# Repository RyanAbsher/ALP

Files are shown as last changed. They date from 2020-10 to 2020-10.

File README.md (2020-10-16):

# ALP

A wireless control system for a balloon-based aerial cave photography lighting platform.

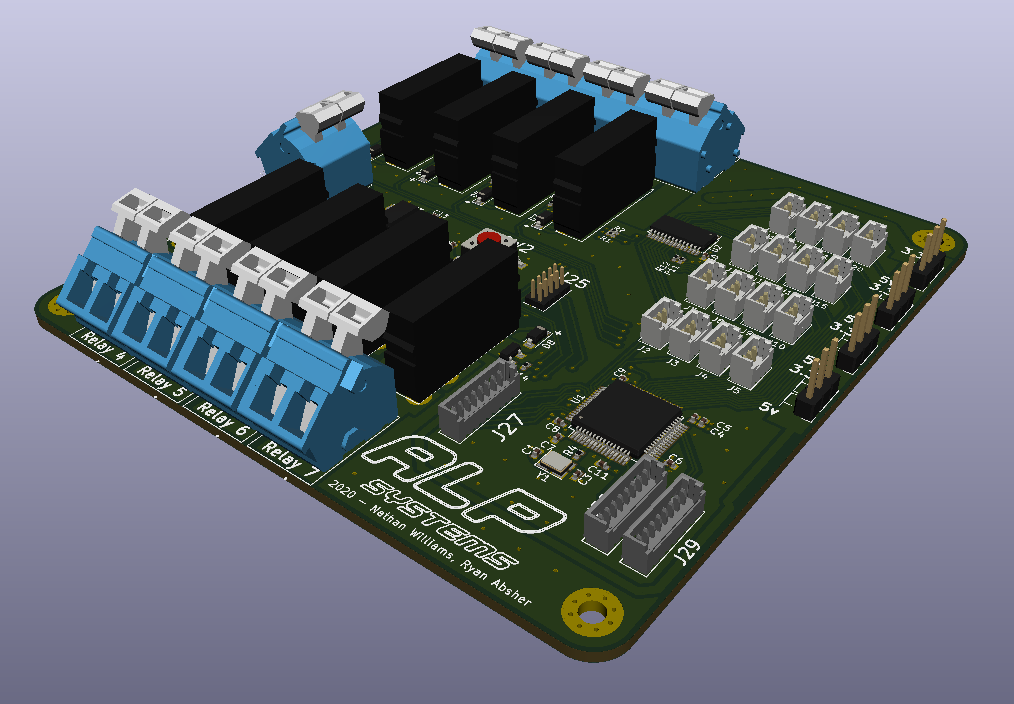
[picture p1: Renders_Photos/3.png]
PCB Render


## Introduction
A friend of mine has for a long time wanted to photograph the top of a particular cave chamber that has never been photographed before. The chamber is 396 feet tall, so access to the top is obviously somewhat limited. In the past they have used a 6' diameter weather balloon to lift lighting to the top, then used telephoto lenses to photograph it from the ground. This time they are putting the cameras on the balloon, but they didn't have a good way to control the equipment from the ground. This project is the solution to that problem.

## Hardware
The board is based on an STM32 microcontroller. There are three different boards needed for this project: 1 on the ballon, and 2 in control boxes on the ground. I have designed this PCB so that the same design can be used for all of the locations. It is also generic enough that it can be adapted if this particular project changes, or if we want to use it for other projects in the future. There are 8 dedicated relay outputs (5A DC Max) and 16 general IO connectors. These can be used as inputs or outputs, and each bank of 4 connectors has a jumper that can be used to select either 5v or 3.3v outputs. Each of these 16 outputs can also optionally be used as a servo output, with a dedicated servo driver IC on-board.

Communication between boards is accomplished using USART. The two control boxes are connected with a cable. The balloon-mounted board uses HC-12 serial radio modules to communicate with the primary control box on the ground. In ground-based tests of these radios we have achieved effective communication over distances greater than 1400 meters. I do not anticipate any problem using them to communicated over ~120 meters.

Users on the ground can use the two control boxes to control various equipment on the balloon. There is a DSLR camera mounted on the balloon, and the ISO, Aperture, and Shutter speed can be set from the ground. The shutter can of course also be triggered from the ground. The DSLR is mounted on a custom pan/tilt servo gimbal, and this is fully controllable from the ground.

There are 3 powerful LED lights mounted on the balloon, these are controlled through some of the relay outputs, and their direction can be controlled with a servo attached to each.

There are various other pieces of hardware that are controllable from the ground, although the configuration and type of such is likely to change as the project continues.

## Prototype
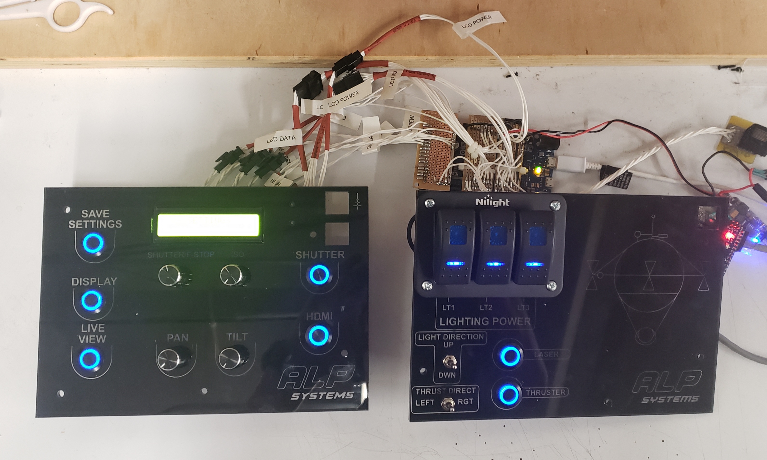
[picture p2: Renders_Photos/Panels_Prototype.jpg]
PCB Render

The photo above contains the laser-etched acrylic control panels, and the stripboard working prototype that I built. While it admittedly doesn't look that great, it did serve it's purpose in that it showed all of the pieces of the system could communicate and function as expected.

## To Do
I have an STM32 dev board on the way that has the same chip that I will be using on this board (STM32F103RBT6). I will use it to confirm that it can do everything I expect of it, then I will be ordering the PCBs. I will likely be ordering them from JLCPCB, and will have them assemble the SMT components on at least a few of the boards. The boards will be populated differently depending on which location they are currently in. For example, the control boxes will not need the relays populated. I will hand-solder the relays and connectors as needed.

Once I have the boards in hand, then I can write the necessary software. I programmed the protoype using the Arduino environment, and I was happy with the way the software worked. Since I have the software mostly completed, it should be fairly simple to port it over to the STM32, likely using STs STM32CubeIDE software. When the software is complete, I will add it to this repository.

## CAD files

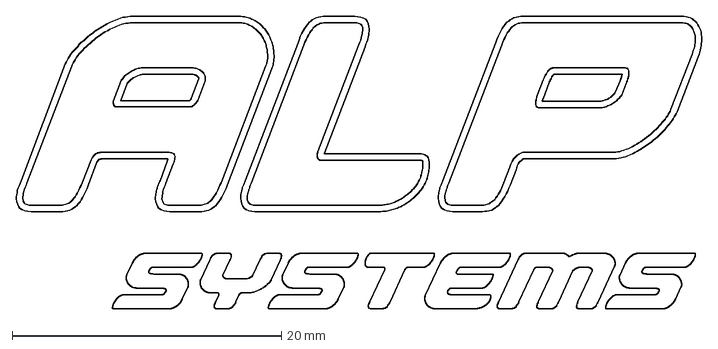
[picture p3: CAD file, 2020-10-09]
logo.dxf
50.9 x 21.7 mm

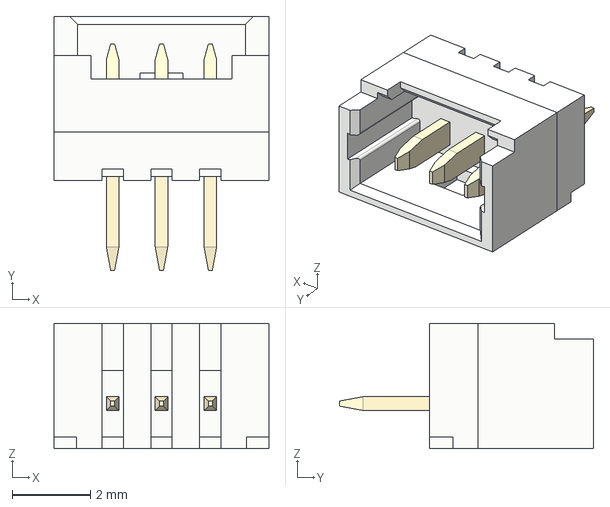
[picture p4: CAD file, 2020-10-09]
Models/Molex_Picoblade_530470310.stp
5.50 x 6.50 x 3.20 mm

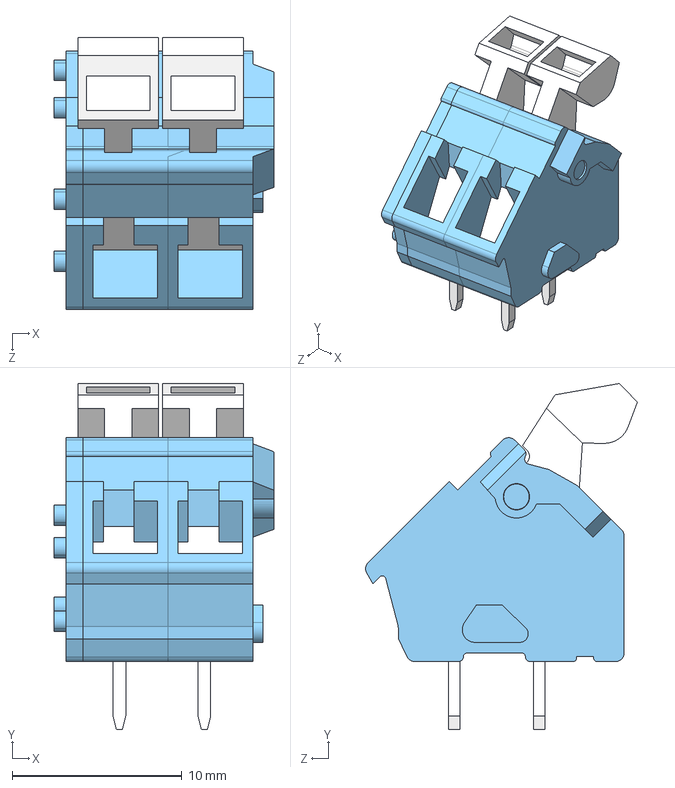
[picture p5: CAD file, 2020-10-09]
Models/CUI_DEVICES_TBL005A-500-02BE-2WT.step
12.9 x 20.4 x 16.0 mm
TBL005A-500 - END CAP_Blue
TBL005A-500 - BODY_Blue x 2
TBL005A-500 - PUSH BUTTON_White x 2

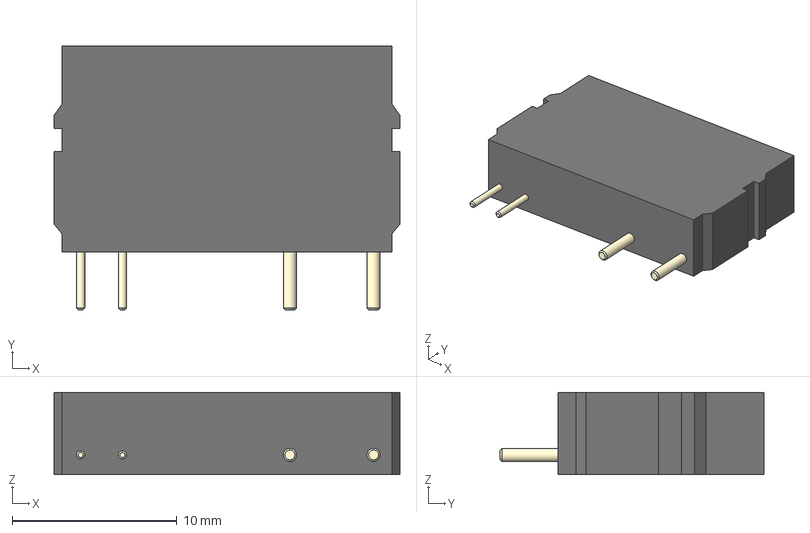
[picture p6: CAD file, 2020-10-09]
Models/APAN3103.step
21.0 x 16.0 x 5.00 mm

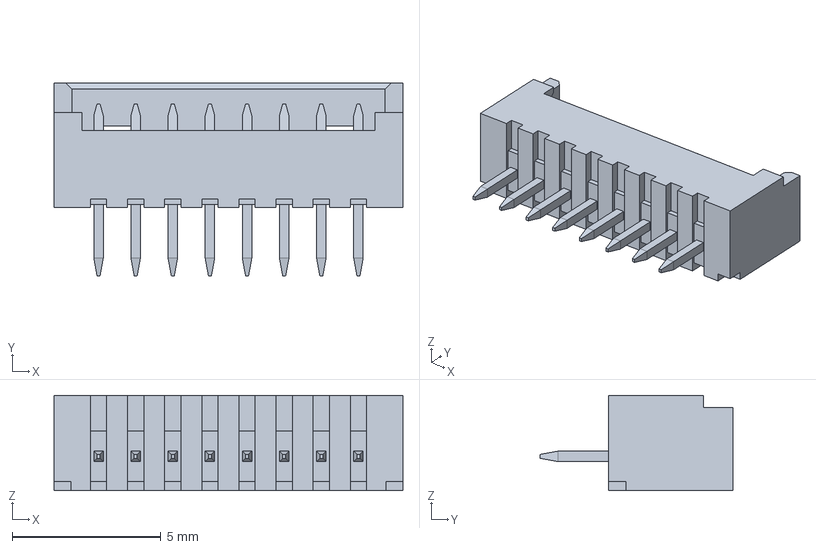
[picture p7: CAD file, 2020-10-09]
Models/Molex_Picoblade_530470810.stp
11.8 x 6.50 x 3.20 mm

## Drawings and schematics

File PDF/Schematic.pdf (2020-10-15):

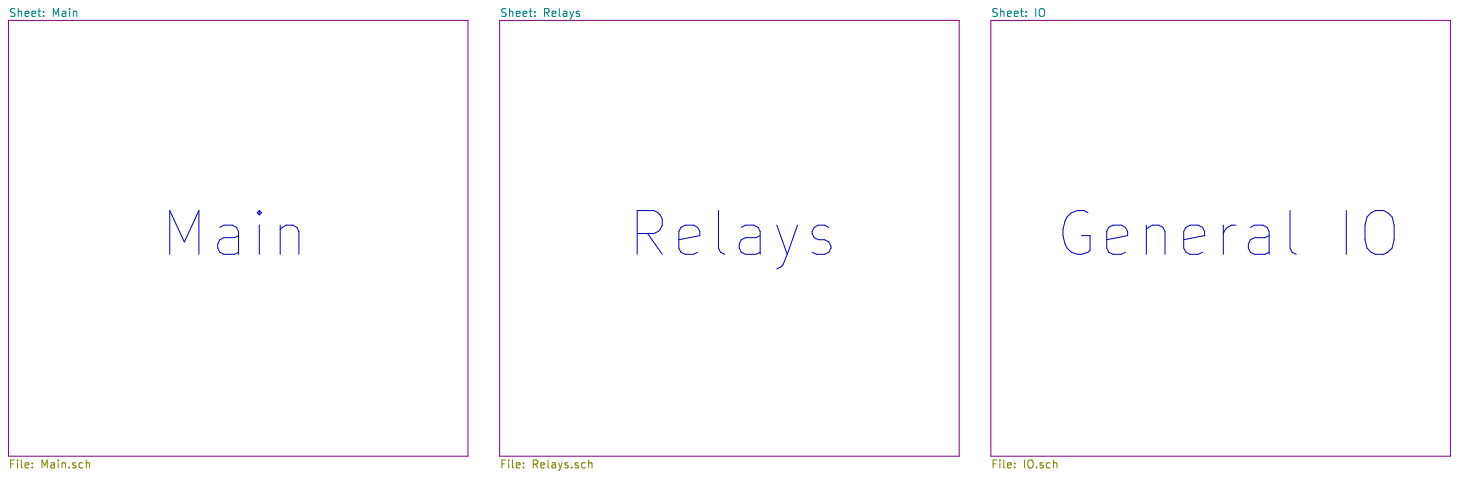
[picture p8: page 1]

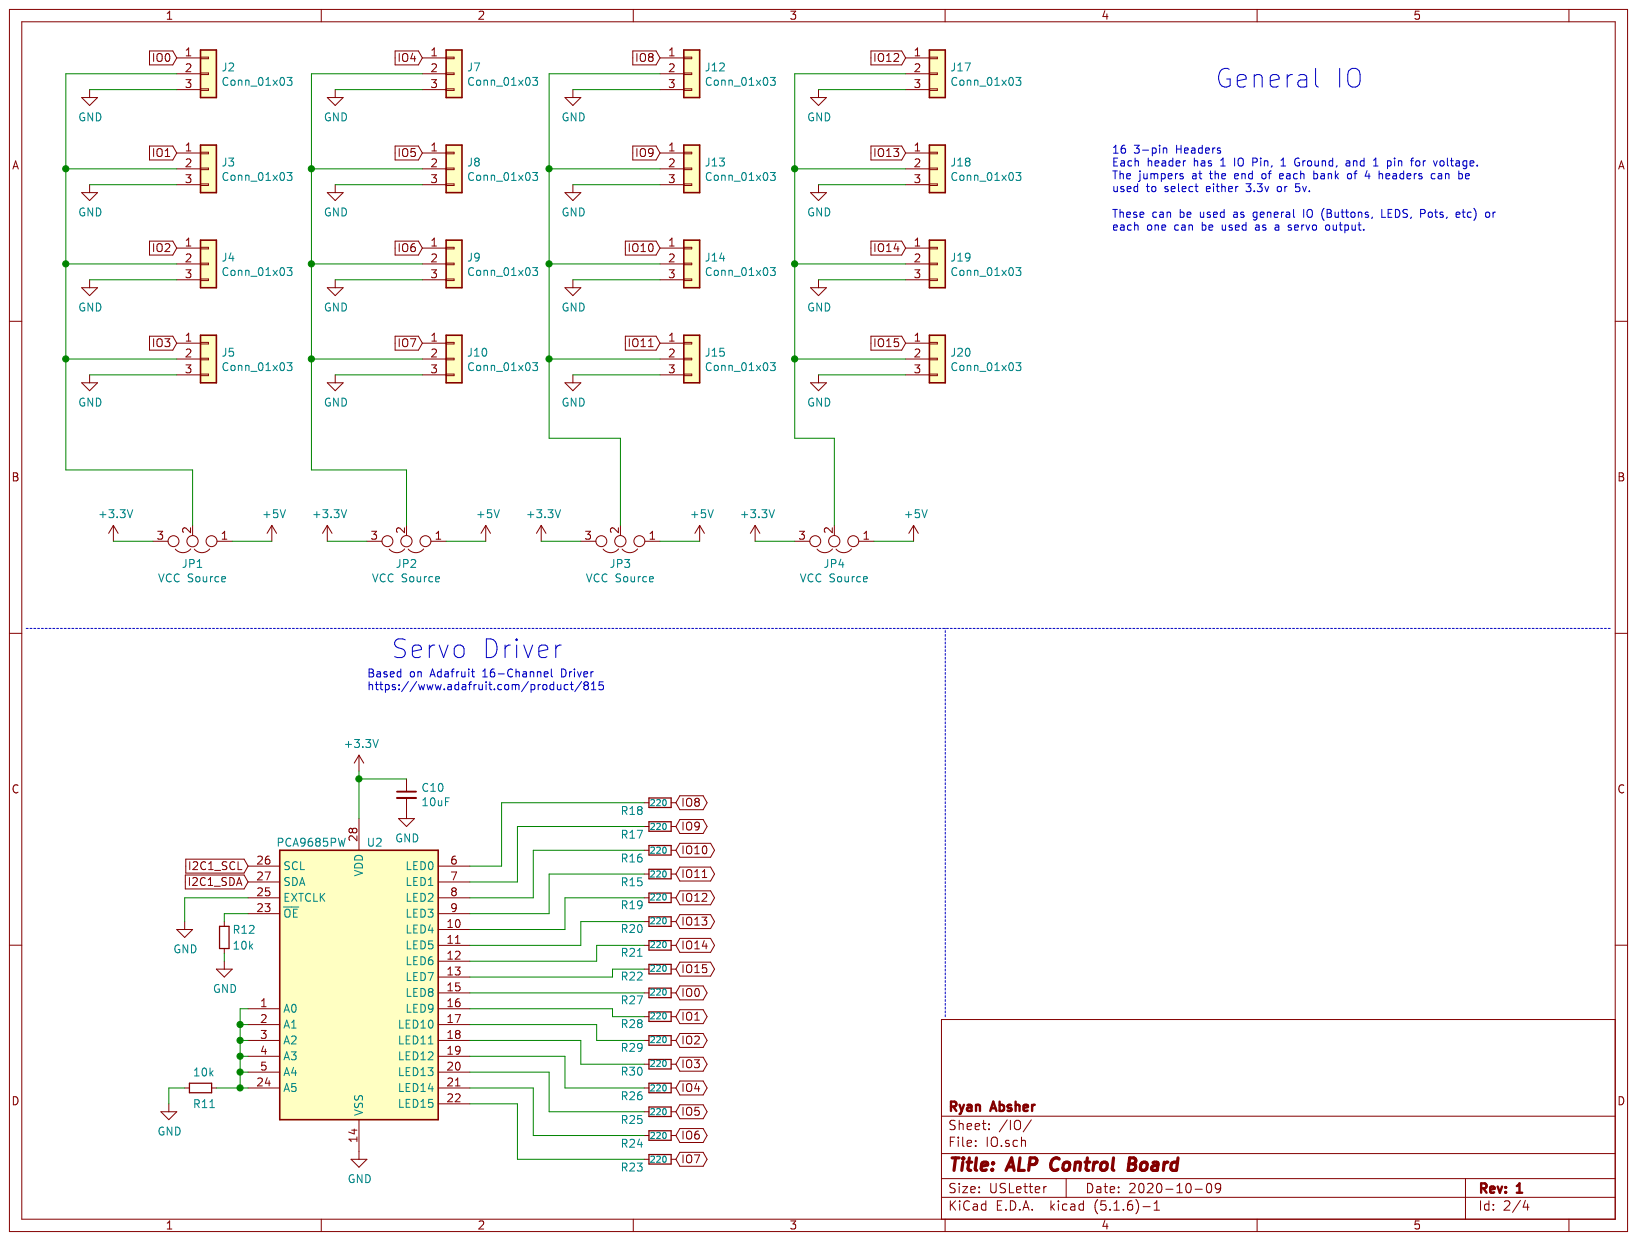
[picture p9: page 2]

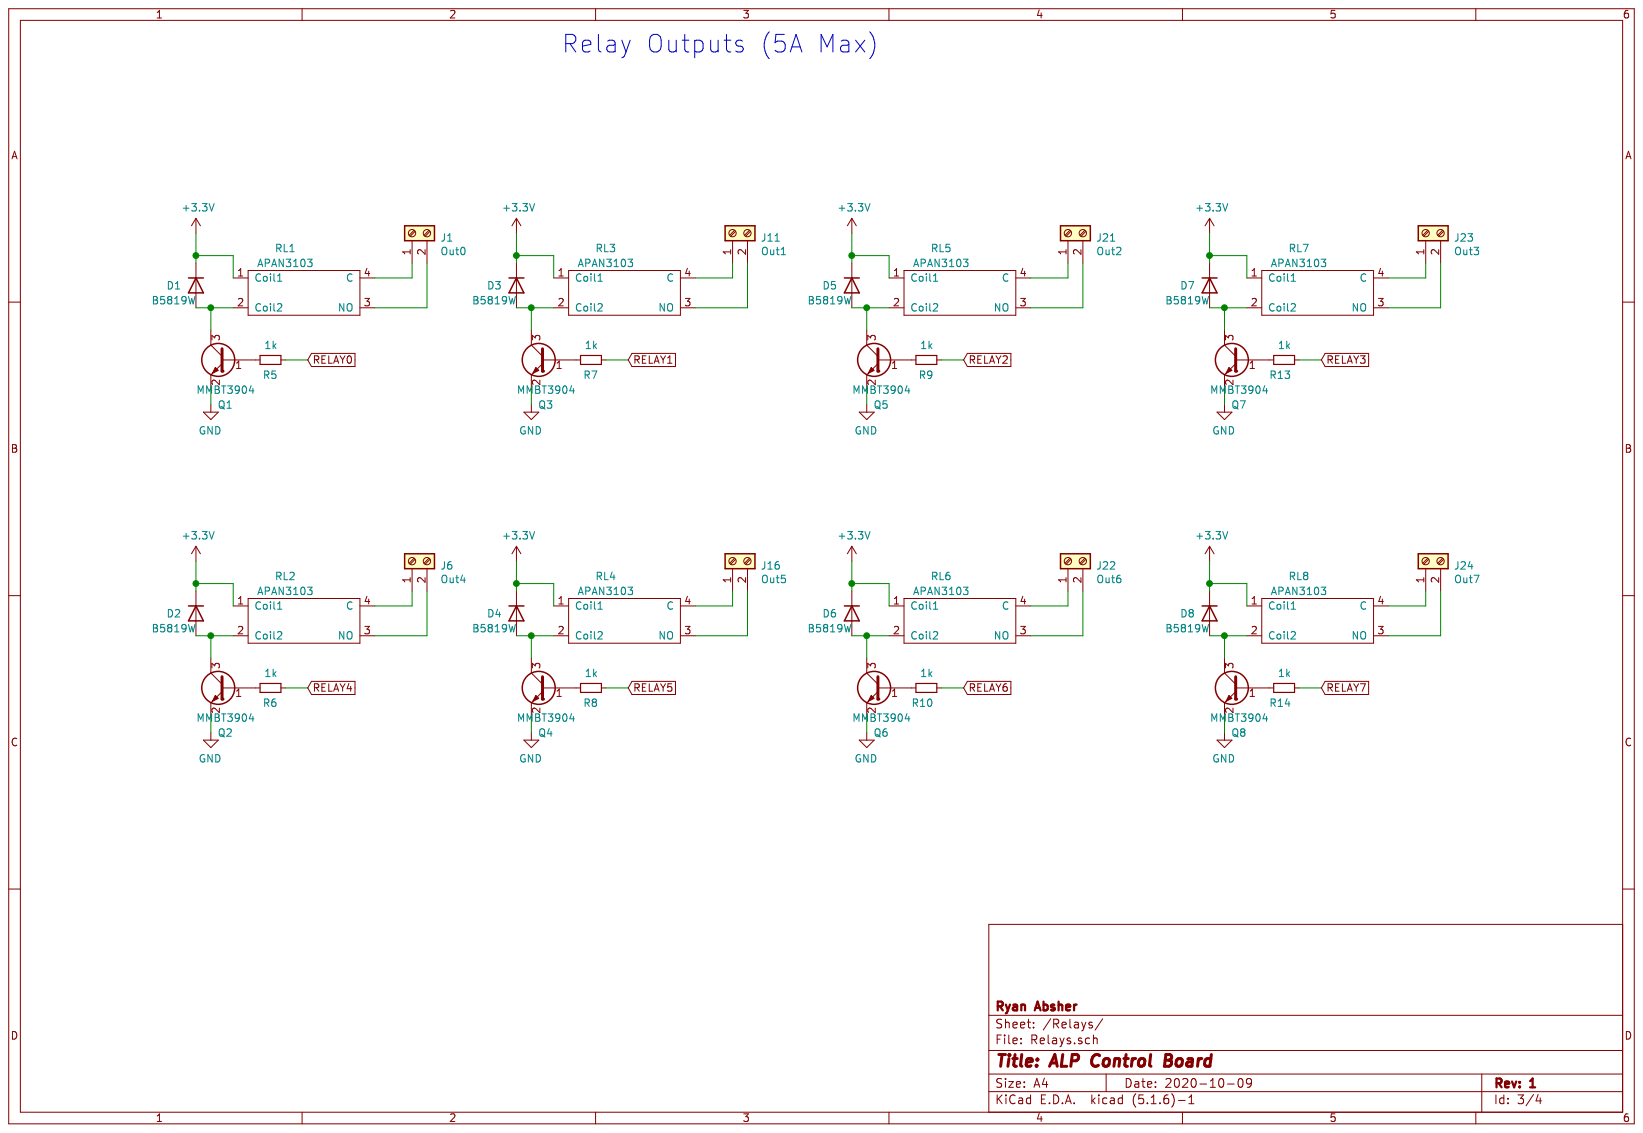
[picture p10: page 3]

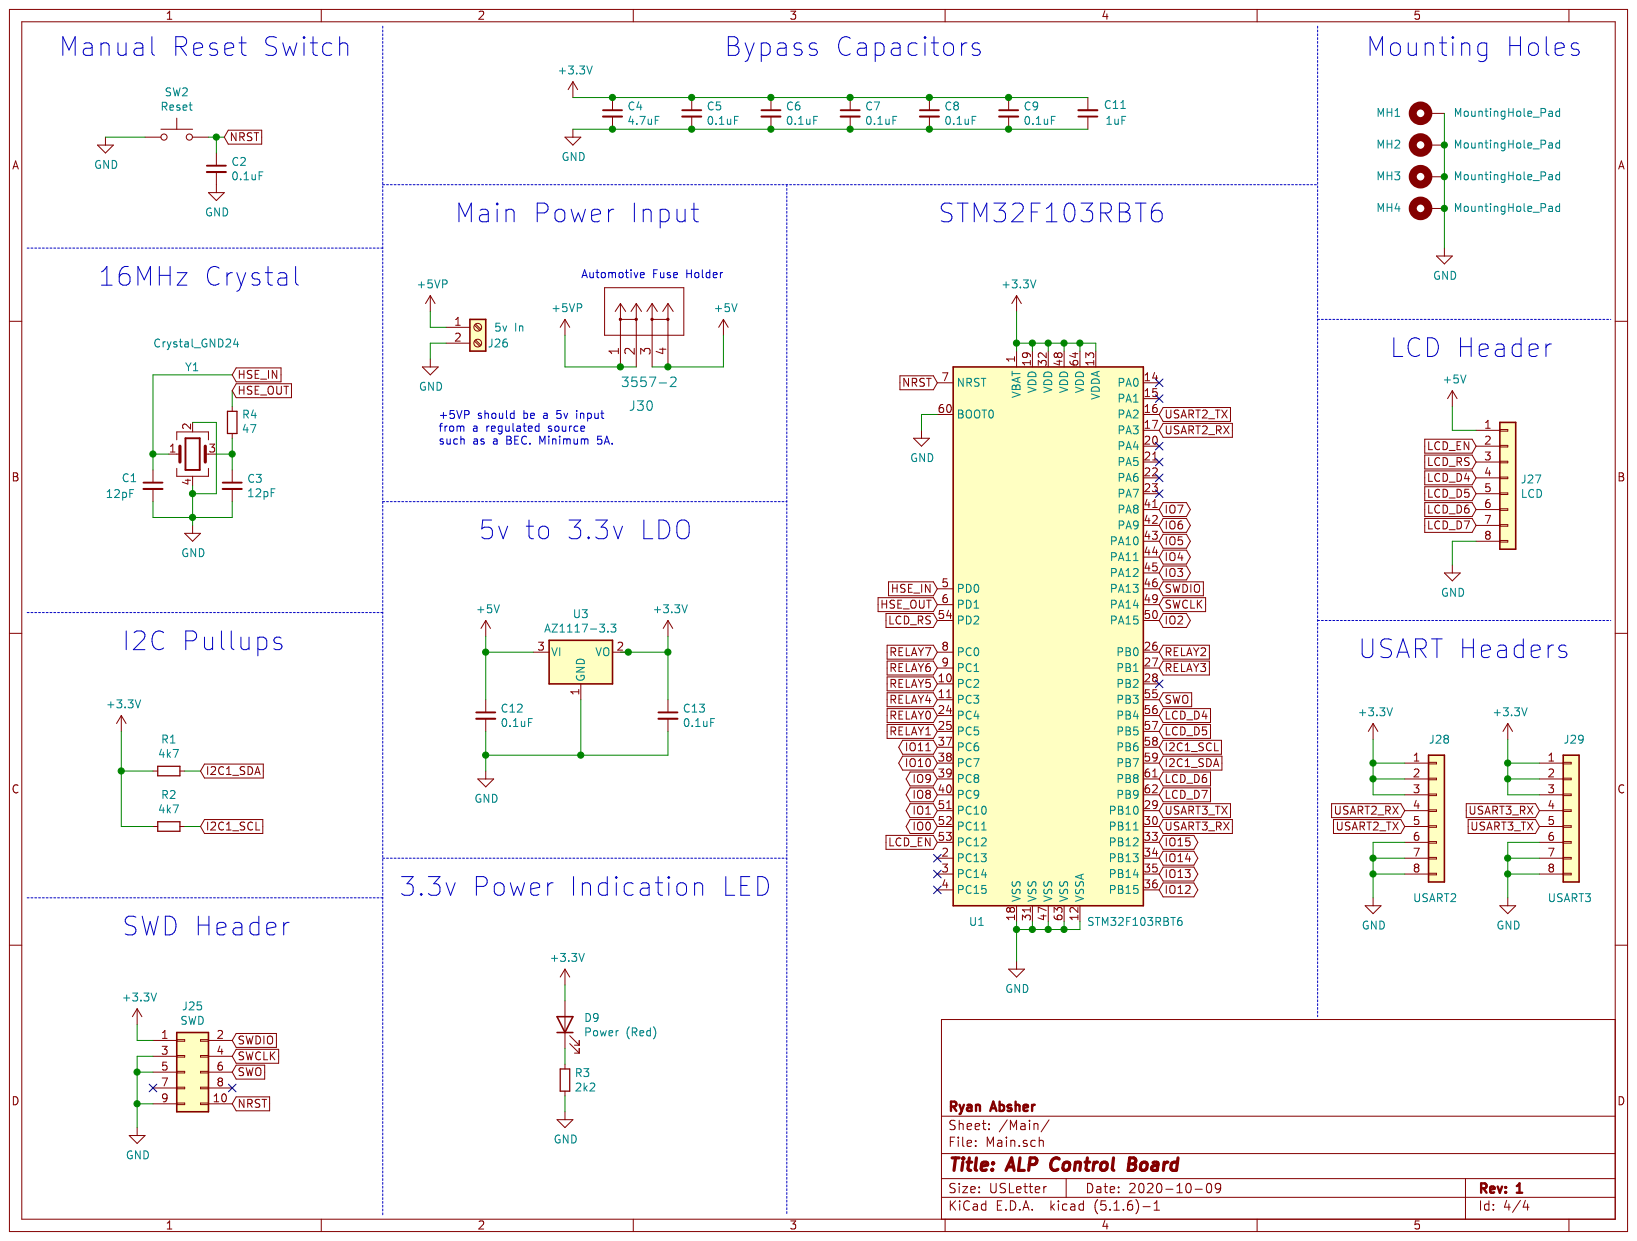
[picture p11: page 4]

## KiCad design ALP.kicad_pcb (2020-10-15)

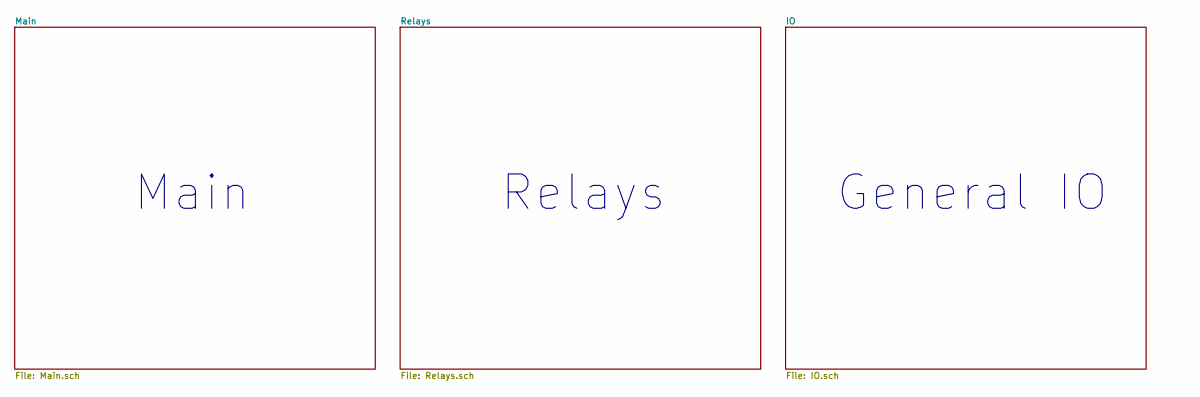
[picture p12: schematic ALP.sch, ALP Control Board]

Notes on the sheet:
General IO
Main
Relays

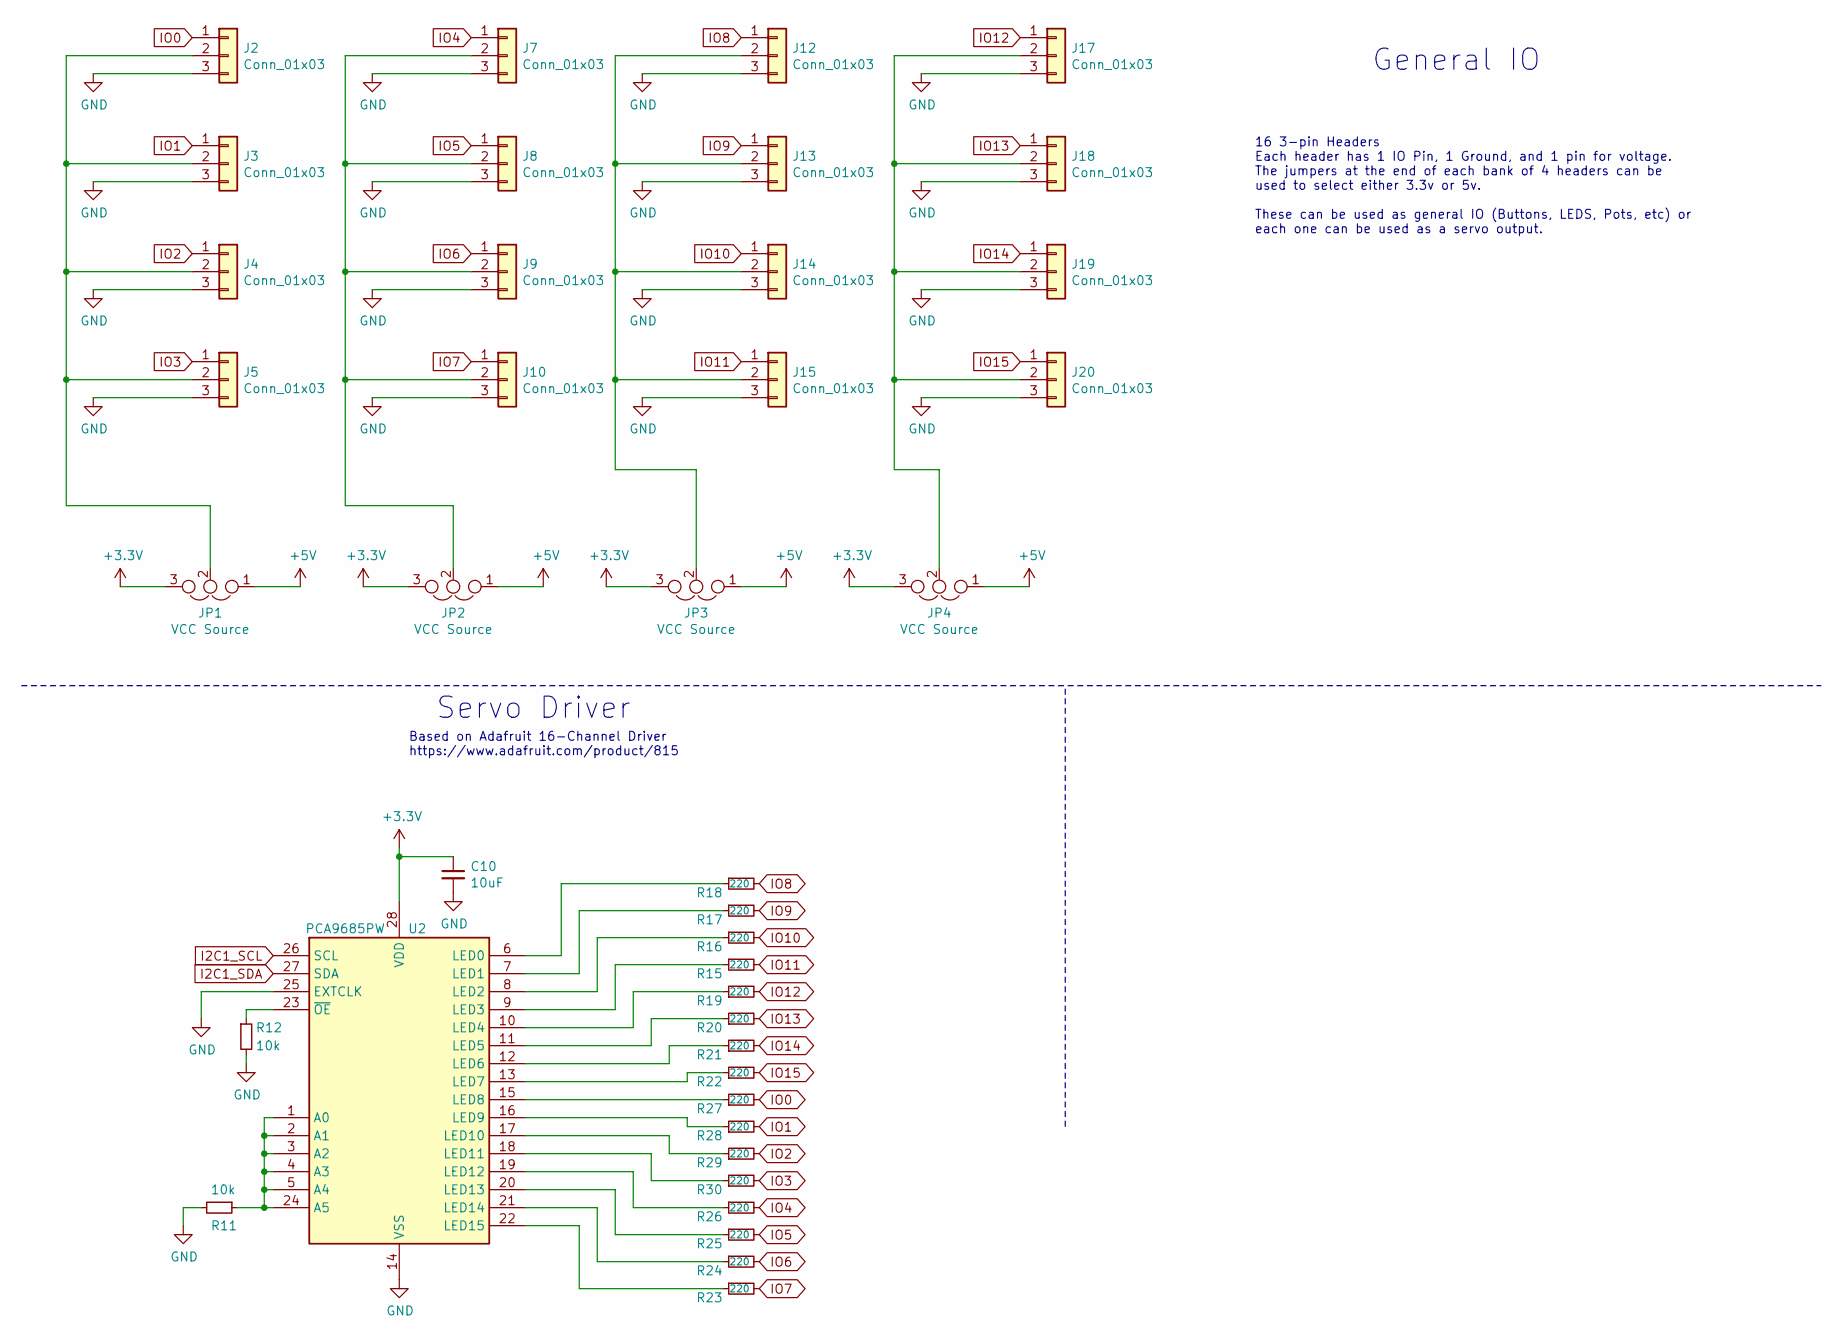
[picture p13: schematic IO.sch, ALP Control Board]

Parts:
C10: 10uF; C_0402_1005Metric; LCSC Part # C15525
J2, J3, J4, J5, J7, J8, J9, J10, J12, J13, J14, J15, J17, J18, J19, J20: Conn_01x03; Molex_PicoBlade_53047-0610_1x03_P1.25mm_Vertical
JP1, JP2, JP3, JP4: VCC Source; PinHeader_1x03_P2.54mm_Vertical
R11, R12: 10k; R_0402_1005Metric; LCSC Part # C25744
R15, R16, R17, R18, R19, R20, R21, R22, R23, R24, R25, R26, R27, R28, R29, R30: 220; R_0402_1005Metric; LCSC Part # C1555
U2: PCA9685PW; TSSOP-28_4.4x9.7mm_P0.65mm; LCSC Part # C92206

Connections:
+3V3: C10.1, JP1.3, JP2.3, JP3.3, JP4.3, U2.28 (VDD); also elsewhere on the board
+5V: JP1.1, JP2.1, JP3.1, JP4.1; also elsewhere on the board
GND: C10.2, J2.3, J3.3, J4.3, J5.3, J7.3, J8.3, J9.3, J10.3, J12.3, J13.3, J14.3, J15.3, J17.3, J18.3, J19.3, J20.3, R11.2, R12.2, U2.14 (VSS), U2.25 (EXTCLK); also elsewhere on the board
I2C1_SCL: U2.26 (SCL); also elsewhere on the board
I2C1_SDA: U2.27 (SDA); also elsewhere on the board
IO0: J2.1, R27.2; also elsewhere on the board
IO1: J3.1, R28.2; also elsewhere on the board
IO2: J4.1, R29.2; also elsewhere on the board
IO3: J5.1, R30.2; also elsewhere on the board
IO4: J7.1, R26.2; also elsewhere on the board
IO5: J8.1, R25.2; also elsewhere on the board
IO6: J9.1, R24.2; also elsewhere on the board
IO7: J10.1, R23.2; also elsewhere on the board
IO8: J12.1, R18.2; also elsewhere on the board
IO9: J13.1, R17.2; also elsewhere on the board
IO10: J14.1, R16.2; also elsewhere on the board
IO11: J15.1, R15.2; also elsewhere on the board
IO12: J17.1, R19.2; also elsewhere on the board
IO13: J18.1, R20.2; also elsewhere on the board
IO14: J19.1, R21.2; also elsewhere on the board
IO15: J20.1, R22.2; also elsewhere on the board
unnamed: J2.2, J3.2, J4.2, J5.2, JP1.2
unnamed: J7.2, J8.2, J9.2, J10.2, JP2.2
unnamed: J12.2, J13.2, J14.2, J15.2, JP3.2
unnamed: J17.2, J18.2, J19.2, J20.2, JP4.2
unnamed: R11.1, U2.1 (A0), U2.2 (A1), U2.3 (A2), U2.4 (A3), U2.5 (A4), U2.24 (A5)
unnamed: R12.1, U2.23 (~OE)
unnamed: R15.1, U2.9 (LED3)
unnamed: R16.1, U2.8 (LED2)
unnamed: R17.1, U2.7 (LED1)
unnamed: R18.1, U2.6 (LED0)
unnamed: R19.1, U2.10 (LED4)
unnamed: R20.1, U2.11 (LED5)
unnamed: R21.1, U2.12 (LED6)
unnamed: R22.1, U2.13 (LED7)
unnamed: R23.1, U2.22 (LED15)
unnamed: R24.1, U2.21 (LED14)
unnamed: R25.1, U2.20 (LED13)
unnamed: R26.1, U2.19 (LED12)
unnamed: R27.1, U2.15 (LED8)
unnamed: R28.1, U2.16 (LED9)
unnamed: R29.1, U2.17 (LED10)
unnamed: R30.1, U2.18 (LED11)

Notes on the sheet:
Servo Driver
Based on Adafruit 16-Channel Driver https://www.adafruit.com/product/815
16 3-pin Headers Each header has 1 IO Pin, 1 Ground, and 1 pin for voltage. The jumpers at the end of each bank of 4 headers can be used to select either 3.3v or 5v. These can be used as general IO (Buttons, LEDS, Pots, etc) or each one can be used as a servo output.
General IO

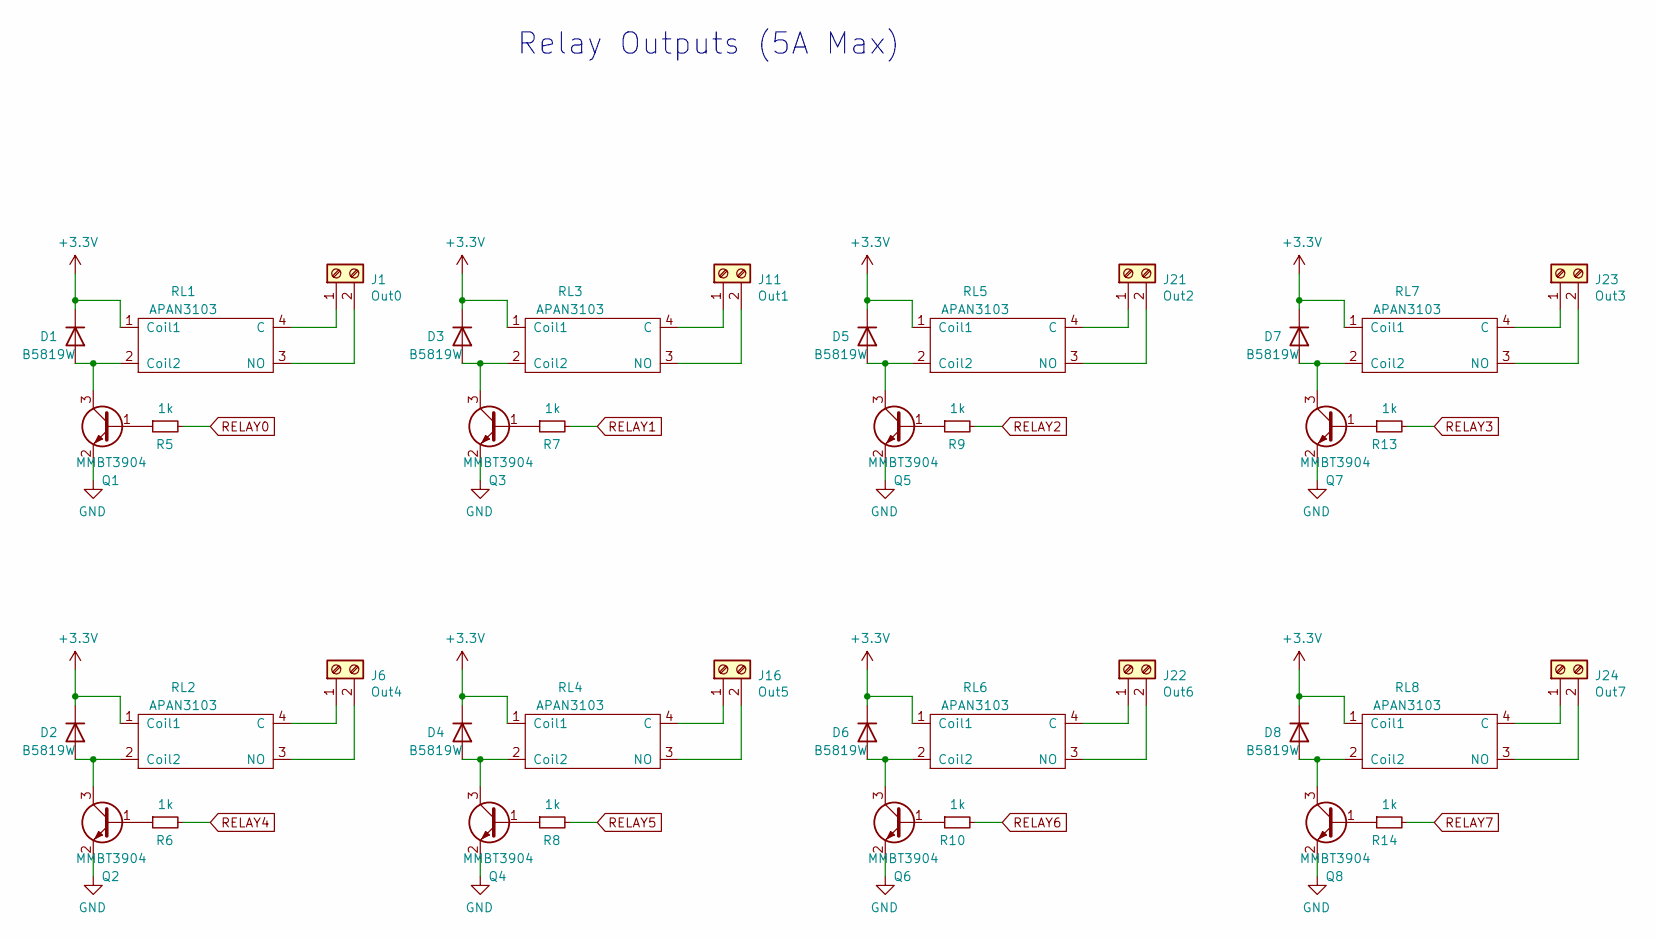
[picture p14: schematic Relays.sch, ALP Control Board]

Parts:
D1, D2, D3, D4, D5, D6, D7, D8: B5819W; D_SOD-123; LCSC PN C81598
J1: Out0; CUI_TBL005A-500-02GY-2WT
J6: Out4; CUI_TBL005A-500-02GY-2WT
J11: Out1; CUI_TBL005A-500-02GY-2WT
J16: Out5; CUI_TBL005A-500-02GY-2WT
J21: Out2; CUI_TBL005A-500-02GY-2WT
J22: Out6; CUI_TBL005A-500-02GY-2WT
J23: Out3; CUI_TBL005A-500-02GY-2WT
J24: Out7; CUI_TBL005A-500-02GY-2WT
Q1, Q2, Q3, Q4, Q5, Q6, Q7, Q8: MMBT3904; SOT-23; LCSC Part # C20526
R5, R6, R7, R8, R9, R10, R13, R14: 1k; R_0402_1005Metric; LCSC Part # C11702
RL1, RL2, RL3, RL4, RL5, RL6, RL7, RL8: APAN3103; APAN1303

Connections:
+3V3: D1.1 (K), D2.1 (K), D3.1 (K), D4.1 (K), D5.1 (K), D6.1 (K), D7.1 (K), D8.1 (K), RL1.1 (Coil1), RL2.1 (Coil1), RL3.1 (Coil1), RL4.1 (Coil1), RL5.1 (Coil1), RL6.1 (Coil1), RL7.1 (Coil1), RL8.1 (Coil1); also elsewhere on the board
GND: Q1.2 (E), Q2.2 (E), Q3.2 (E), Q4.2 (E), Q5.2 (E), Q6.2 (E), Q7.2 (E), Q8.2 (E); also elsewhere on the board
unnamed: D1.2 (A), Q1.3 (C), RL1.2 (Coil2)
unnamed: D2.2 (A), Q2.3 (C), RL2.2 (Coil2)
unnamed: D3.2 (A), Q3.3 (C), RL3.2 (Coil2)
unnamed: D4.2 (A), Q4.3 (C), RL4.2 (Coil2)
unnamed: D5.2 (A), Q5.3 (C), RL5.2 (Coil2)
unnamed: D6.2 (A), Q6.3 (C), RL6.2 (Coil2)
unnamed: D7.2 (A), Q7.3 (C), RL7.2 (Coil2)
unnamed: D8.2 (A), Q8.3 (C), RL8.2 (Coil2)
unnamed: J1.1, RL1.4 (C)
unnamed: J1.2, RL1.3 (NO)
unnamed: J6.1, RL2.4 (C)
unnamed: J6.2, RL2.3 (NO)
unnamed: J11.1, RL3.4 (C)
unnamed: J11.2, RL3.3 (NO)
unnamed: J16.1, RL4.4 (C)
unnamed: J16.2, RL4.3 (NO)
unnamed: J21.1, RL5.4 (C)
unnamed: J21.2, RL5.3 (NO)
unnamed: J22.1, RL6.4 (C)
unnamed: J22.2, RL6.3 (NO)
unnamed: J23.1, RL7.4 (C)
unnamed: J23.2, RL7.3 (NO)
unnamed: J24.1, RL8.4 (C)
unnamed: J24.2, RL8.3 (NO)
unnamed: Q1.1 (B), R5.1
unnamed: Q2.1 (B), R6.1
unnamed: Q3.1 (B), R7.1
unnamed: Q4.1 (B), R8.1
unnamed: Q5.1 (B), R9.1
unnamed: Q6.1 (B), R10.1
unnamed: Q7.1 (B), R13.1
unnamed: Q8.1 (B), R14.1
RELAY0: R5.2; also elsewhere on the board
RELAY1: R7.2; also elsewhere on the board
RELAY2: R9.2; also elsewhere on the board
RELAY3: R13.2; also elsewhere on the board
RELAY4: R6.2; also elsewhere on the board
RELAY5: R8.2; also elsewhere on the board
RELAY6: R10.2; also elsewhere on the board
RELAY7: R14.2; also elsewhere on the board

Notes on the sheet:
Relay Outputs (5A Max)

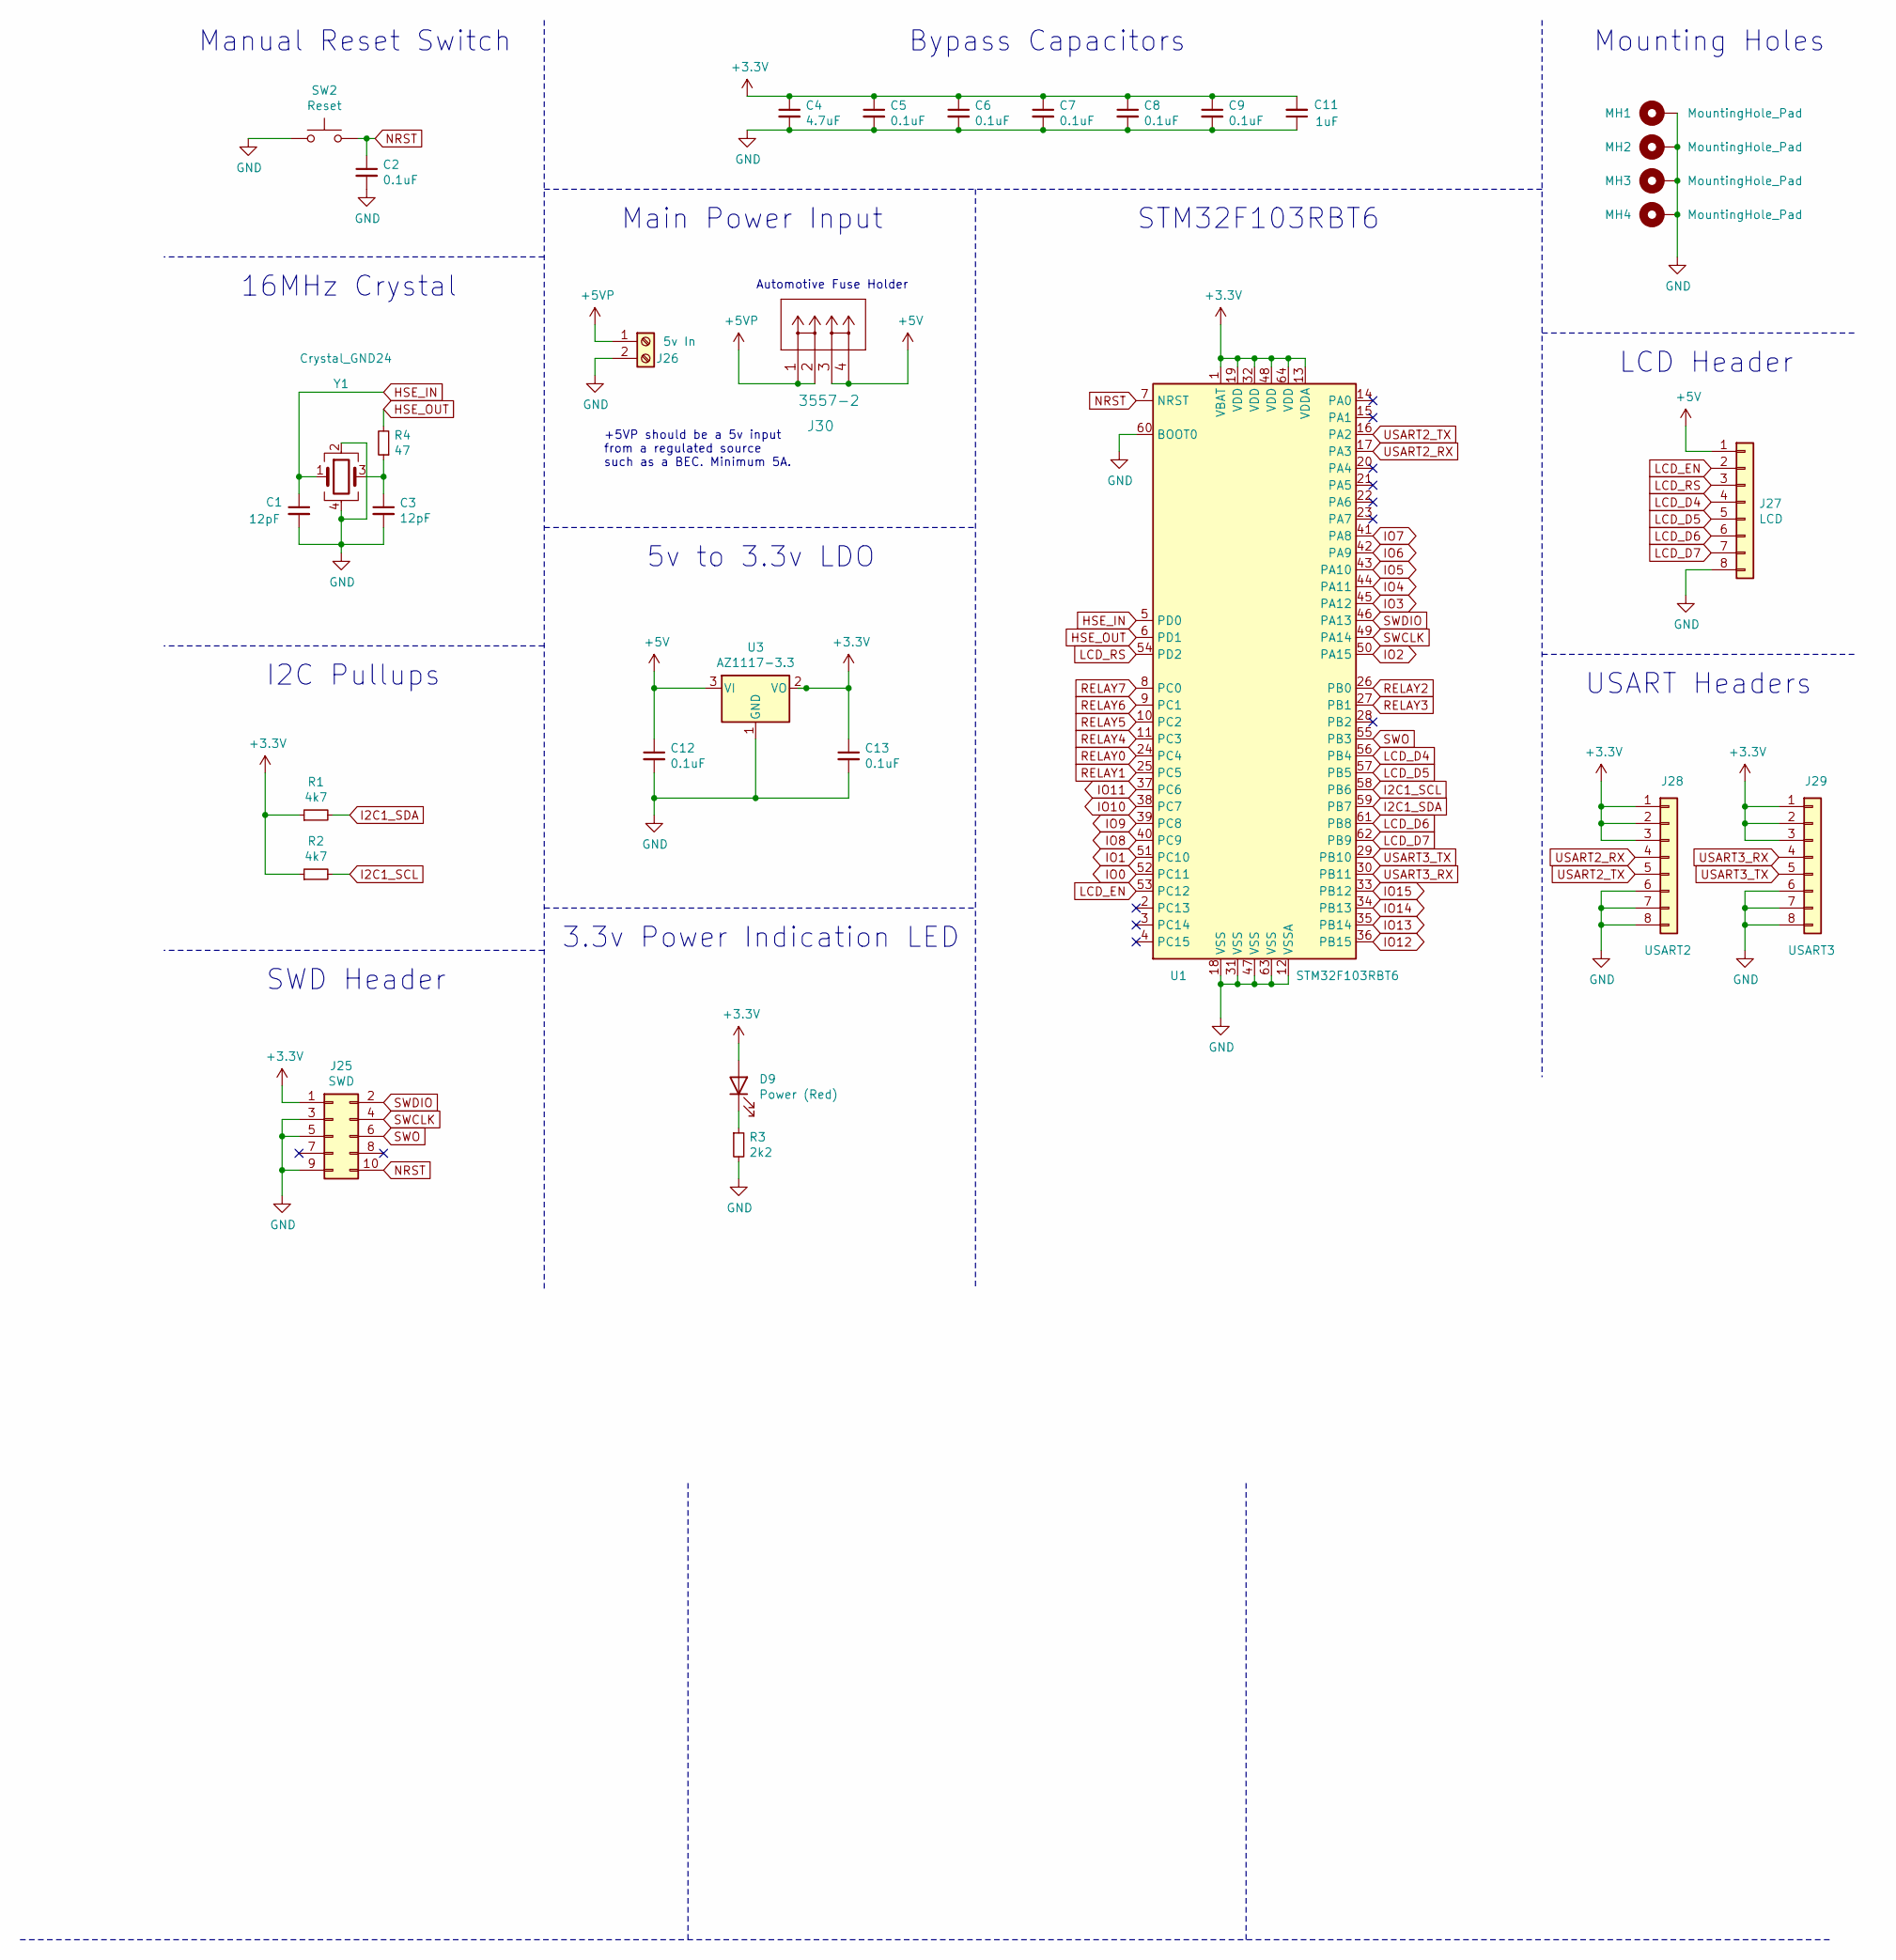
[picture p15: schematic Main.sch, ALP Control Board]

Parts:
C1, C3: 12pF; C_0402_1005Metric; LCSC Part # C1547
C2, C5, C6, C7, C8, C9, C12, C13: 0.1uF; C_0402_1005Metric; LCSC Part # C1525
C4: 4.7uF; C_0402_1005Metric; LCSC Part # C23733
C11: 1uF; C_0402_1005Metric; LCSC Part # C52923
D9: Power (Red); LED_0603_1608Metric; LCSC Part # C2286
J25: SWD; PinHeader_2x05_P1.27mm_Vertical
J26: 5v In; CUI_TBL005A-500-02GY-2WT
J27: LCD; Molex_PicoBlade_53047-0810_1x08_P1.25mm_Vertical
J28: USART2; Molex_PicoBlade_53047-0810_1x08_P1.25mm_Vertical
J29: USART3; Molex_PicoBlade_53047-0810_1x08_P1.25mm_Vertical
J30: 3557-2
MH1, MH2, MH3, MH4: MountingHole_Pad; MountingHole_3mm_Pad_Via
R1, R2: 4k7; R_0402_1005Metric; LCSC Part # C25900
R3: 2k2; R_0402_1005Metric; LCSC Part # C25879
R4: 47; R_0402_1005Metric; LCSC Part # C25118
SW2: Reset; SW_SPST_PTS645
U1: STM32F103RBT6; LQFP-64_10x10mm_P0.5mm; LCSC Part # C8735
U3: AZ1117-3.3; SOT-223-3_TabPin2; LCSC Part # C6186
Y1: Crystal_GND24; Crystal_SMD_3225-4Pin_3.2x2.5mm; LCSC Part # C13738

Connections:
+3V3: C4.1, C5.1, C6.1, C7.1, C8.1, C9.1, C11.2, C13.1, D9.2 (A), J25.1, J28.1, J28.2, J28.3, J29.1, J29.2, J29.3, R1.1, R2.1, U1.1 (VBAT), U1.13 (VDDA), U1.19 (VDD), U1.32 (VDD), U1.48 (VDD), U1.64 (VDD), U3.2 (VO); also elsewhere on the board
+5V: C12.1, J27.1, J30.3, J30.4, U3.3 (VI); also elsewhere on the board
+5VP: J26.1, J30.1, J30.2
GND: C1.2, C2.2, C3.2, C4.2, C5.2, C6.2, C7.2, C8.2, C9.2, C11.1, C12.2, C13.2, J25.3, J25.5, J25.9, J26.2, J27.8, J28.6, J28.7, J28.8, J29.6, J29.7, J29.8, MH1.1, MH2.1, MH3.1, MH4.1, R3.2, SW2.1, U1.12 (VSSA), U1.18 (VSS), U1.31 (VSS), U1.47 (VSS), U1.60 (BOOT0), U1.63 (VSS), U3.1 (GND), Y1.2, Y1.4; also elsewhere on the board
HSE_IN: C1.1, U1.5 (PD0), Y1.1
HSE_OUT: R4.2, U1.6 (PD1)
I2C1_SCL: R2.2, U1.58 (PB6); also elsewhere on the board
I2C1_SDA: R1.2, U1.59 (PB7); also elsewhere on the board
IO0: U1.52 (PC11); also elsewhere on the board
IO1: U1.51 (PC10); also elsewhere on the board
IO2: U1.50 (PA15); also elsewhere on the board
IO3: U1.45 (PA12); also elsewhere on the board
IO4: U1.44 (PA11); also elsewhere on the board
IO5: U1.43 (PA10); also elsewhere on the board
IO6: U1.42 (PA9); also elsewhere on the board
IO7: U1.41 (PA8); also elsewhere on the board
IO8: U1.40 (PC9); also elsewhere on the board
IO9: U1.39 (PC8); also elsewhere on the board
IO10: U1.38 (PC7); also elsewhere on the board
IO11: U1.37 (PC6); also elsewhere on the board
IO12: U1.36 (PB15); also elsewhere on the board
IO13: U1.35 (PB14); also elsewhere on the board
IO14: U1.34 (PB13); also elsewhere on the board
IO15: U1.33 (PB12); also elsewhere on the board
LCD_D4: J27.4, U1.56 (PB4)
LCD_D5: J27.5, U1.57 (PB5)
LCD_D6: J27.6, U1.61 (PB8)
LCD_D7: J27.7, U1.62 (PB9)
LCD_EN: J27.2, U1.53 (PC12)
LCD_RS: J27.3, U1.54 (PD2)
NRST: C2.1, J25.10, SW2.2, U1.7 (NRST)
unnamed: C3.1, R4.1, Y1.3
unnamed: D9.1 (K), R3.1
RELAY0: U1.24 (PC4); also elsewhere on the board
RELAY1: U1.25 (PC5); also elsewhere on the board
RELAY2: U1.26 (PB0); also elsewhere on the board
RELAY3: U1.27 (PB1); also elsewhere on the board
RELAY4: U1.11 (PC3); also elsewhere on the board
RELAY5: U1.10 (PC2); also elsewhere on the board
RELAY6: U1.9 (PC1); also elsewhere on the board
RELAY7: U1.8 (PC0); also elsewhere on the board
SWCLK: J25.4, U1.49 (PA14)
SWDIO: J25.2, U1.46 (PA13)
SWO: J25.6, U1.55 (PB3)
USART2_RX: J28.4, U1.17 (PA3)
USART2_TX: J28.5, U1.16 (PA2)
USART3_RX: J29.4, U1.30 (PB11)
USART3_TX: J29.5, U1.29 (PB10)

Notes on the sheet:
Manual Reset Switch
16MHz Crystal
SWD Header
I2C Pullups
Mounting Holes
LCD Header
USART Headers
Bypass Capacitors
5v to 3.3v LDO
Automotive Fuse Holder
Main Power Input
3.3v Power Indication LED
+5VP should be a 5v input from a regulated source such as a BEC. Minimum 5A.
STM32F103RBT6

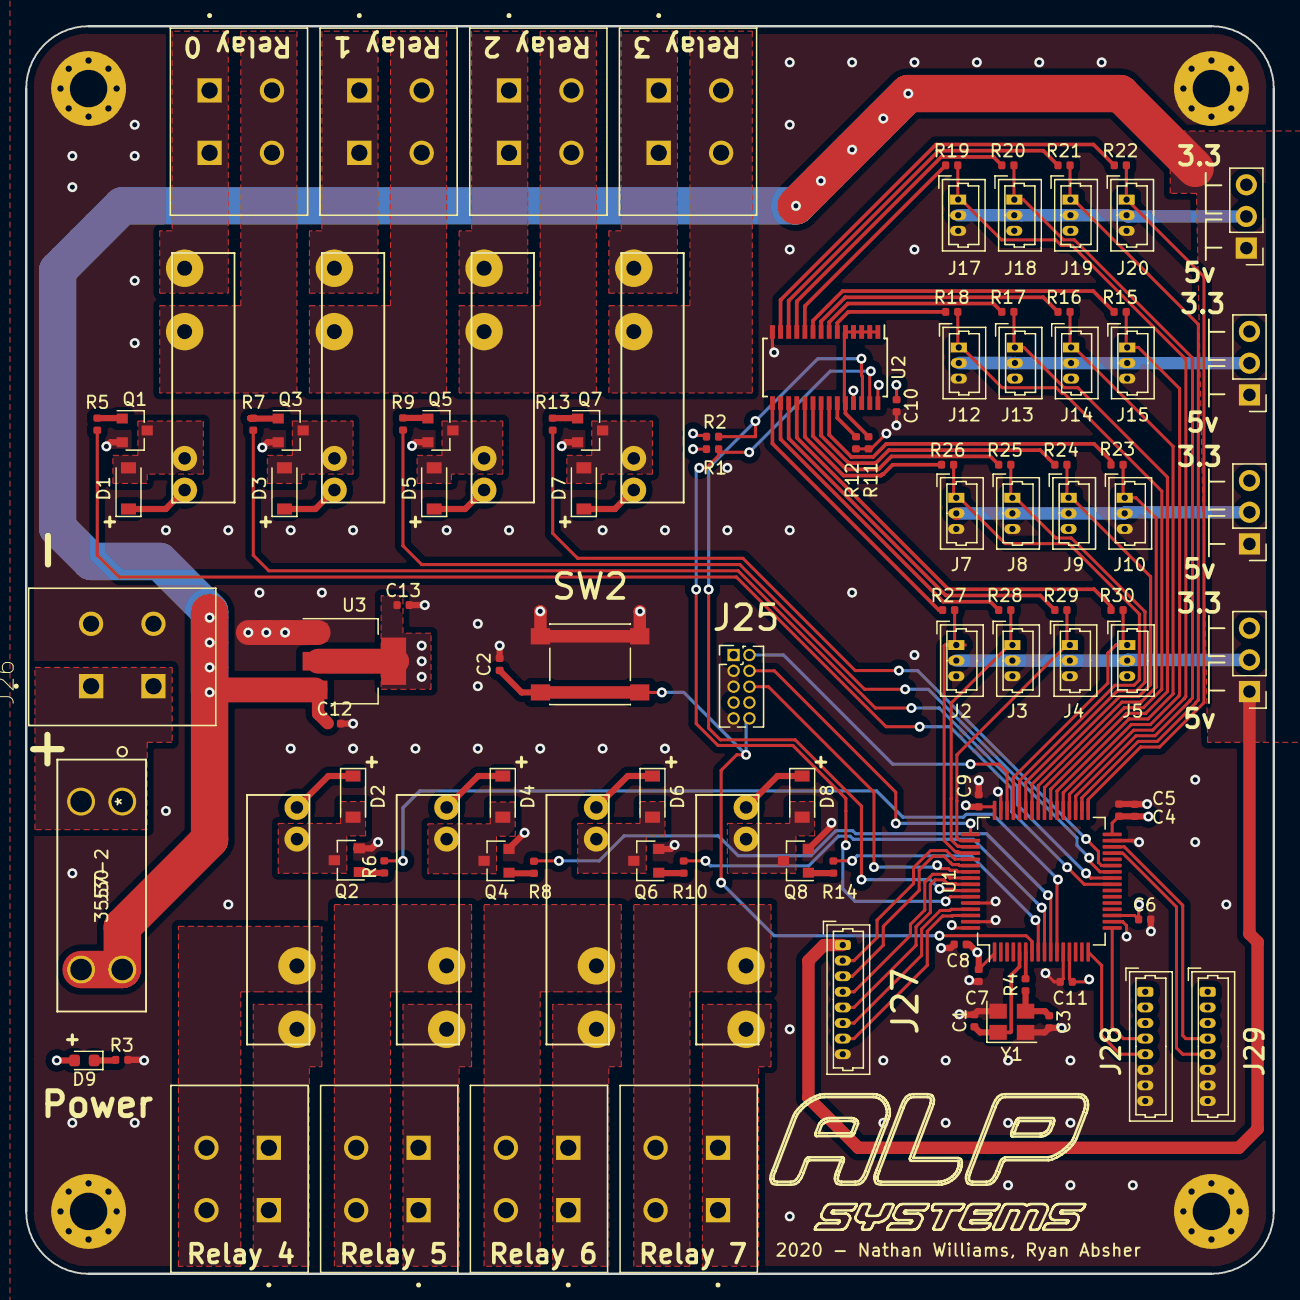
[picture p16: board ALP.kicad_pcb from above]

Board: 4 copper layers, 100.0 x 100.0 mm, 111 parts (0 on the bottom side), 102 nets.

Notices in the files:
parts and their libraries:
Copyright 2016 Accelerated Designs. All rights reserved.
